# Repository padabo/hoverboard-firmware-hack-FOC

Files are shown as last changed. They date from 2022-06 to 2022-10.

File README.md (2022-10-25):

# hoverboard-firmware-hack-FOC




This repository implements Field Oriented Control (FOC) for stock hoverboards. Compared to the commutation method, this new FOC control method offers superior performance featuring:
 - reduced noise and vibrations 	
 - smooth torque output and improved motor efficiency. Thus, lower energy consumption
 - field weakening to increase maximum speed range

Table of Contents
=======================

* **Wiki:** please check the wiki pages for [Getting Started](https://github.com/EFeru/hoverboard-firmware-hack-FOC/wiki#getting-started) and for [Troubleshooting](https://github.com/EFeru/hoverboard-firmware-hack-FOC/wiki#troubleshooting)
* [Hardware](#hardware)
* [FOC Firmware](#foc-firmware)
* [Example Variants](#example-variants)
* [Projects and Links](#projects-and-links)
* [Contributions](#contributions)

#### The hoverboards with mainboards also come with 2 sideboards(not [splitboards](https://github.com/EFeru/hoverboard-firmware-hack-FOC/wiki/Firmware-Compatibility#split-boards)), check the following [wiki](https://github.com/EFeru/hoverboard-firmware-hack-FOC/wiki/Sideboards) about this firmware

#### For the FOC controller design, see the following repository:
 - [bldc-motor-control-FOC](https://github.com/EFeru/bldc-motor-control-FOC)

#### Videos:
<table>
  <tr>
    <td></td>
    <td></td>
    <td></td>
  </tr>
  <tr>
    <td></td> 
    <td></td>       
    <td></td>
  </tr>
</table>

---
## Hardware
 
mainboard_pinout

The original Hardware supports two 4-pin cables that originally were connected to the two sideboards. They break out GND, 12/15V and USART2&3 of the Hoverboard mainboard. Both USART2&3 support UART, PWM, PPM, and iBUS input. Additionally, the USART2 can be used as 12bit ADC, while USART3 can be used for I2C. Note that while USART3 (right sideboard cable) is 5V tolerant, USART2 (left sideboard cable) is **not** 5V tolerant.

Typically, the mainboard brain is an [STM32F103RCT6](/docs/literature/[10]_STM32F103xC_datasheet.pdf), however some mainboards feature a [GD32F103RCT6](/docs/literature/[11]_GD32F103xx-Datasheet-Rev-2.7.pdf) which is also supported by this firmware.

For the reverse-engineered schematics of the mainboard, see [20150722_hoverboard_sch.pdf](/docs/20150722_hoverboard_sch.pdf)

---
## FOC Firmware
 
In this firmware 3 control types are available, it can be set in config.h file via CTRL_TYP_SEL parameter:
- Commutation (COM_CTRL)
- Sinusoidal (SIN_CTRL)
- Field Oriented Control (FOC_CTRL) with the following 3 control modes that can be set in config.h file with parameter CTRL_MOD_REQ:
  - **VOLTAGE MODE(VLT_MODE)**: in this mode the controller applies a constant Voltage to the motors. Recommended for robotics applications or applications where a fast motor response is required.
  - **SPEED MODE(SPD_MODE)**: in this mode a closed-loop controller realizes the input speed RPM target by rejecting any of the disturbance (resistive load) applied to the motor. Recommended for robotics applications or constant speed applications.
  - **TORQUE MODE(TRQ_MODE)**: in this mode the input torque target is realized. This mode enables motor "freewheeling" when the torque target is `0`. Recommended for most applications with a sitting human driver.

#### Comparison between different control methods

|Control method| Complexity | Efficiency | Smoothness | Field Weakening | Freewheeling | Standstill hold |
|--|--|--|--|--|--|--|
|Commutation| - | - | ++ | n.a. | n.a. | + |
|Sinusoidal| + | ++ | ++ | +++ | n.a. | + |
|FOC VOLTAGE| ++ | +++ | ++ | ++ | n.a. | +<sup>(2)</sup> |
|FOC SPEED| +++ | +++ | + | ++ | n.a. | +++ |
|FOC TORQUE| +++ | +++ | +++ | ++ | +++<sup>(1)</sup> | n.a<sup>(2)</sup> |

<sup>(1)</sup> By enabling `ELECTRIC_BRAKE_ENABLE` in `config.h`, the freewheeling amount can be adjusted using the `ELECTRIC_BRAKE_MAX` parameter.<br/>
<sup>(2)</sup> The standstill hold functionality can be forced by enabling `STANDSTILL_HOLD_ENABLE` in `config.h`. 

In all FOC control modes, the controller features maximum motor speed and maximum motor current protection. This brings great advantages to fulfil the needs of many robotic applications while maintaining safe operation.

### Field Weakening / Phase Advance

 - By default the Field weakening is disabled. You can enable it in config.h file by setting the FIELD_WEAK_ENA = 1 
 - The Field Weakening is a linear interpolation from 0 to FIELD_WEAK_MAX or PHASE_ADV_MAX (depeding if FOC or SIN is selected, respectively)
 - The Field Weakening starts engaging at FIELD_WEAK_LO and reaches the maximum value at FIELD_WEAK_HI
 - The figure below shows different possible calibrations for Field Weakening / Phase Advance
 Field Weakening 
 - If you re-calibrate the Field Weakening please take all the safety measures! The motors can spin very fast!

### Parameters
 - All the calibratable motor parameters can be found in the 'BLDC_controller_data.c'. I provided you with an already calibrated controller, but if you feel like fine tuning it feel free to do so 
 - The parameters are represented in Fixed-point data type for a more efficient code execution
 - For calibrating the fixed-point parameters use the [Fixed-Point Viewer](https://github.com/EFeru/FixedPointViewer) tool
 - The controller parameters are given in [this table](https://github.com/EFeru/bldc-motor-control-FOC/blob/master/02_Figures/paramTable.png)

### FOC Webview

To explore the controller without a Matlab/Simulink installation click on the link below:

[https://eferu.github.io/bldc-motor-control-FOC/](https://eferu.github.io/bldc-motor-control-FOC/)

---
## Example Variants

- **VARIANT_ADC**: The motors are controlled by two potentiometers connected to the Left sensor cable (long wired)
- **VARIANT_USART**: The motors are controlled via serial protocol (e.g. on USART3 right sensor cable, the short wired cable). The commands can be sent from an Arduino. Check out the [hoverserial.ino](/Arduino/hoverserial) as an example sketch.
- **VARIANT_NUNCHUK**: Wii Nunchuk offers one hand control for throttle, braking and steering. This was one of the first input device used for electric armchairs or bottle crates.
- **VARIANT_PPM**: RC remote control with PPM Sum signal.
- **VARIANT_PWM**: RC remote control with PWM signal.
- **VARIANT_IBUS**: RC remote control with Flysky iBUS protocol connected to the Left sensor cable.
- **VARIANT_HOVERCAR**: The motors are controlled by two pedals brake and throttle. Reverse is engaged by double tapping on the brake pedal at standstill. See [HOVERCAR wiki](https://github.com/EFeru/hoverboard-firmware-hack-FOC/wiki/Variant-HOVERCAR).
- **VARIANT_HOVERBOARD**: The mainboard reads the two sideboards data. The sideboards need to be flashed with the hacked version. The balancing controller is **not** yet implemented.
- **VARIANT_TRANSPOTTER**: This is for transpotter build, which is a hoverboard based transportation system. For more details on how to build it check [here](https://github.com/NiklasFauth/hoverboard-firmware-hack/wiki/Build-Instruction:-TranspOtter) and [here](https://hackaday.io/project/161891-transpotter-ng).
- **VARIANT_SKATEBOARD**: This is for skateboard build, controlled using an RC remote with PWM signal connected to the right sensor cable.

Of course the firmware can be further customized for other needs or projects.

---
## Projects and Links

- **Original firmware:** [https://github.com/lucysrausch/hoverboard-firmware-hack](https://github.com/lucysrausch/hoverboard-firmware-hack)
- **[Candas](https://github.com/Candas1/) Hoverboard Web Serial Control:** [https://github.com/Candas1/Hoverboard-Web-Serial-Control](https://github.com/Candas1/Hoverboard-Web-Serial-Control)
- **[RoboDurden's](https://github.com/RoboDurden) online compiler:** [https://pionierland.de/hoverhack/](https://pionierland.de/hoverhack/) 
- **Hoverboard hack for AT32F403RCT6 mainboards:** [https://github.com/cloidnerux/hoverboard-firmware-hack](https://github.com/cloidnerux/hoverboard-firmware-hack)
- **Hoverboard hack for split mainboards:** [https://github.com/flo199213/Hoverboard-Firmware-Hack-Gen2](https://github.com/flo199213/Hoverboard-Firmware-Hack-Gen2)
- **Hoverboard hack from BiPropellant:** [https://github.com/bipropellant](https://github.com/bipropellant)
- **Hoverboard breakout boards:** [https://github.com/Jana-Marie/hoverboard-breakout](https://github.com/Jana-Marie/hoverboard-breakout)

<a/>

- **Bobbycar** [https://github.com/larsmm/hoverboard-firmware-hack-FOC-bbcar](https://github.com/larsmm/hoverboard-firmware-hack-FOC-bbcar)
- **Wheel chair:** [https://github.com/Lahorde/steer_speed_ctrl](https://github.com/Lahorde/steer_speed_ctrl)
- **TranspOtterNG:** [https://github.com/Jan--Henrik/transpOtterNG](https://github.com/Jan--Henrik/transpOtterNG)
- **Hoverboard driver for ROS:** [https://github.com/alex-makarov/hoverboard-driver](https://github.com/alex-makarov/hoverboard-driver)
- **Ongoing OneWheel project:** [https://forum.esk8.news/t/yet-another-hoverboard-to-onewheel-project/60979/14](https://forum.esk8.news/t/yet-another-hoverboard-to-onewheel-project/60979/14)
- **ST Community:** [Custom FOC motor control](https://community.st.com/s/question/0D50X0000B28qTDSQY/custom-foc-control-current-measurement-dma-timer-interrupt-needs-review)

<a/>

- **Telegram Community:** If you are an enthusiast join our [Hooover Telegram Group](https://t.me/joinchat/BHWO_RKu2LT5ZxEkvUB8uw)

---
## Stargazers

Stargazers over time (https://starchart.cc/EFeru/hoverboard-firmware-hack-FOC)

---
## Contributions

Every contribution to this repository is highly appreciated! Feel free to create pull requests to improve this firmware as ultimately you are going to help everyone. 

If you want to donate to keep this firmware updated, please use the link below:



---

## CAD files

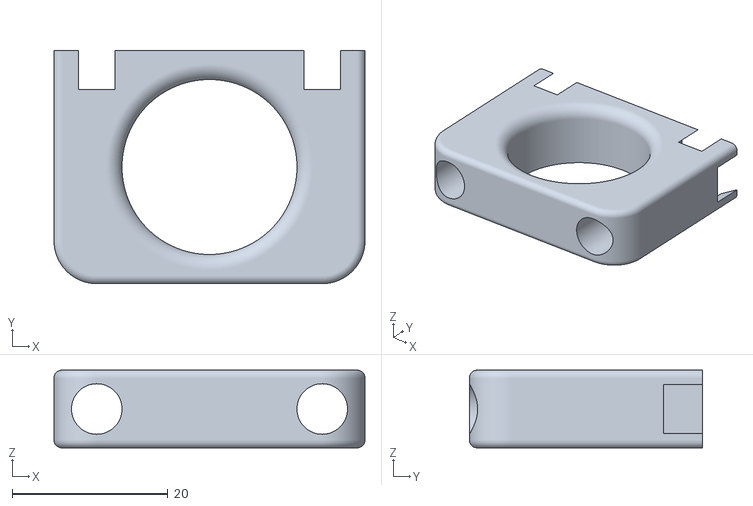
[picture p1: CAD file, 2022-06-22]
Bobbycar STLs/Bobbycar Versteifung x2-x6.stl
40.0 x 30.0 x 10.0

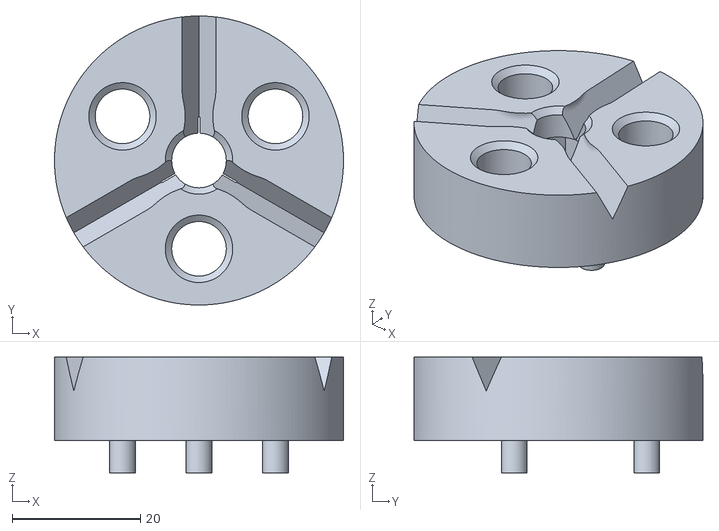
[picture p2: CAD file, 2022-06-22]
Bobbycar STLs/Bobbycar Lenkung Adapter Unten.stl
45.0 x 45.0 x 18.0

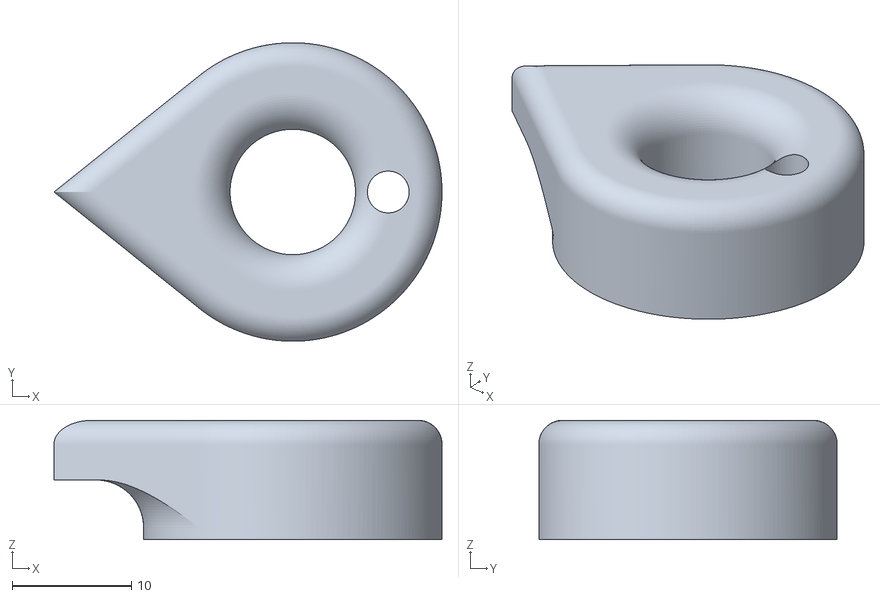
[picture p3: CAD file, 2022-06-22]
Bobbycar STLs/Bobbycar Lenkwinkelsensor Bohradapter.stl
32.5 x 25.0 x 10.0

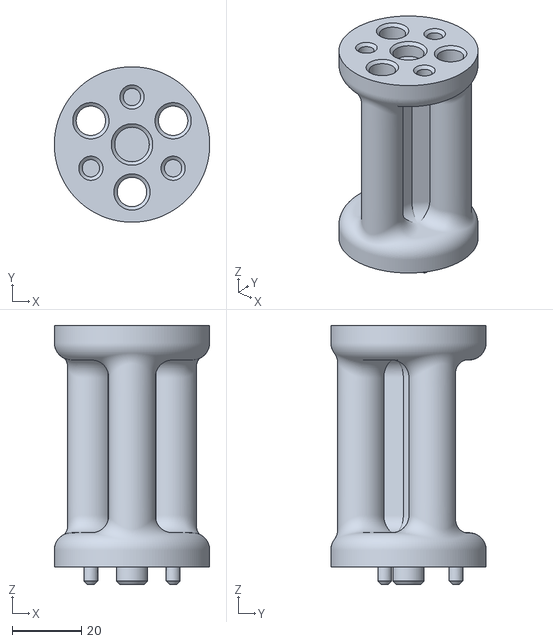
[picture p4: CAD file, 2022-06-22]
Bobbycar STLs/Bobbycar Lenkung Spacer Lang.stl
45.0 x 45.0 x 75.0

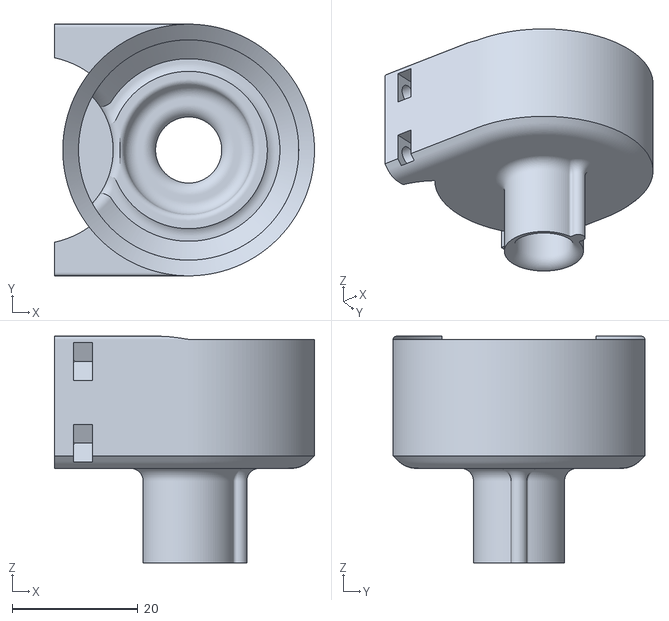
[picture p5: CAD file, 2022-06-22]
Bobbycar STLs/Bobbycar Lenkwinkelsensor Gehäuse.stl
41.3 x 40.0 x 36.0

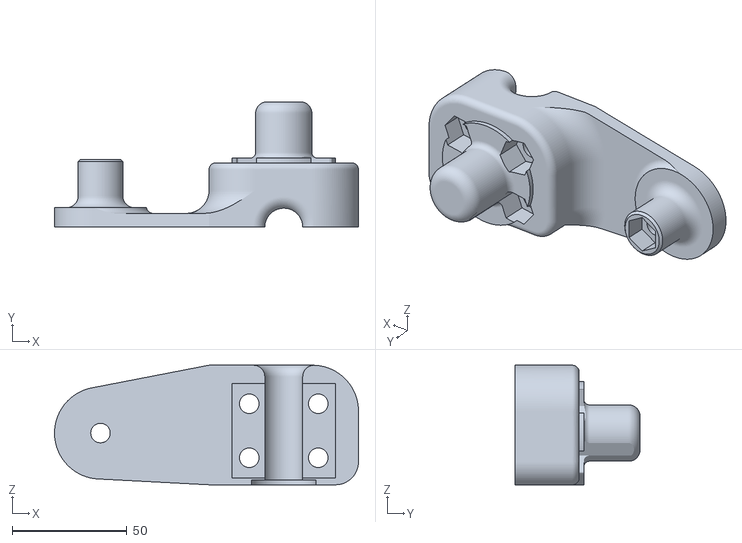
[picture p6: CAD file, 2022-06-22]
Bobbycar STLs/Bobbycar Vorderachse Radaufnahme Oben.stl
132.2 x 54.5 x 52.0

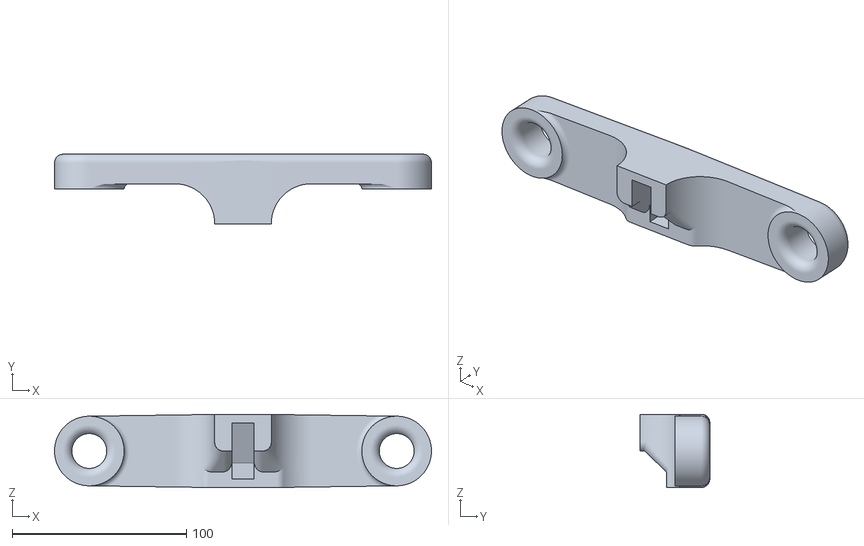
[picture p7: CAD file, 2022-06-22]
Bobbycar STLs/Bobbycar Lenkung Spurstange.stl
216.5 x 40.0 x 42.0

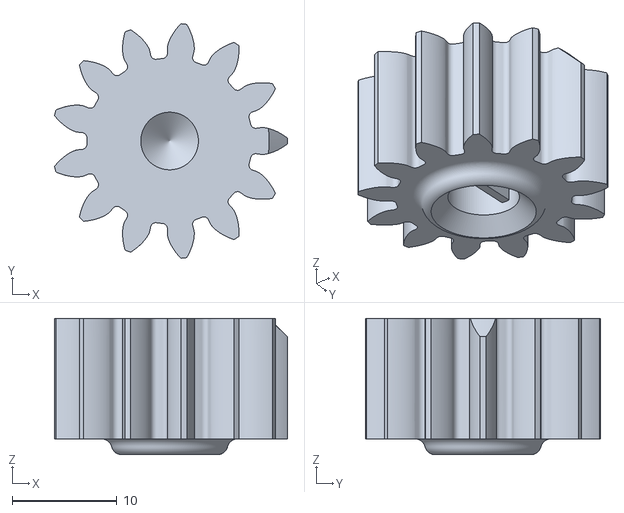
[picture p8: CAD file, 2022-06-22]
Bobbycar STLs/Bobbycar Lenkwinkelsensor Zahnrad Poti.stl
22.2 x 22.4 x 13.0

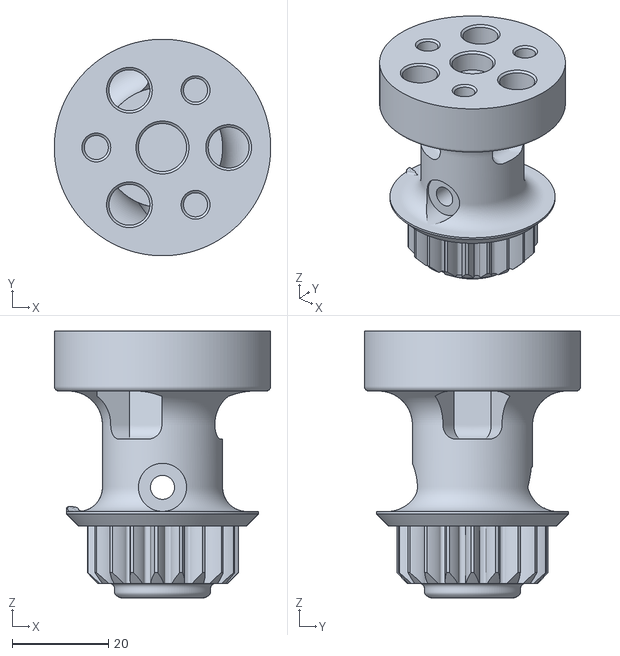
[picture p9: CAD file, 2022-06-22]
Bobbycar STLs/Bobbycar Lenkwinkelsensor Lenkstange.stl
45.0 x 45.0 x 55.5

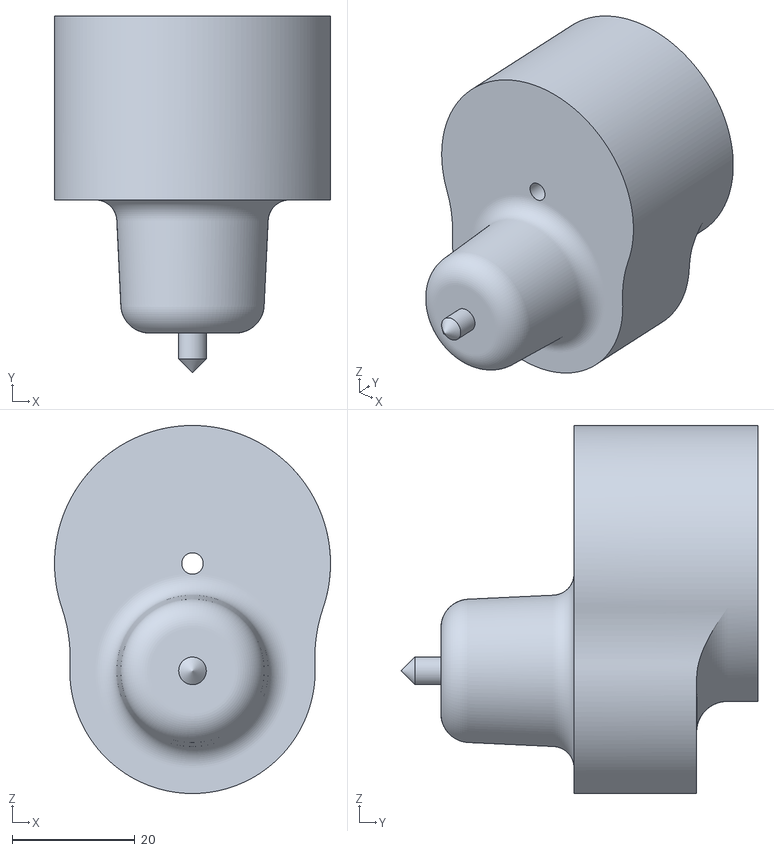
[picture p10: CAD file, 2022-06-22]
Bobbycar STLs/Bobbycar New Adapter x2.stl
45.0 x 58.2 x 60.0

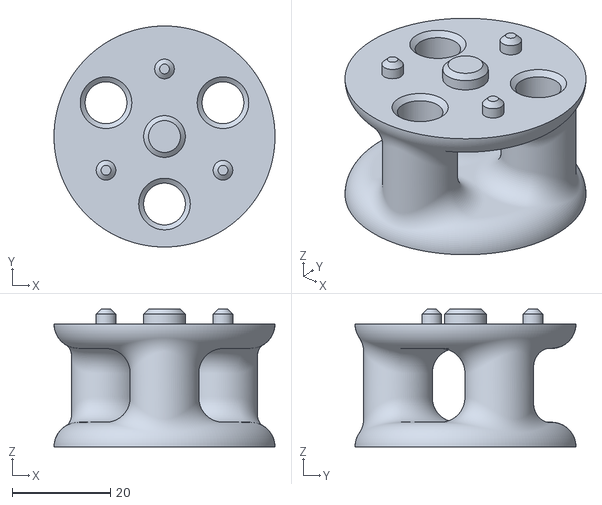
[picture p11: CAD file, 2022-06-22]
Bobbycar STLs/Bobbycar Lenkung Spacer Kurz.stl
45.0 x 45.0 x 28.0

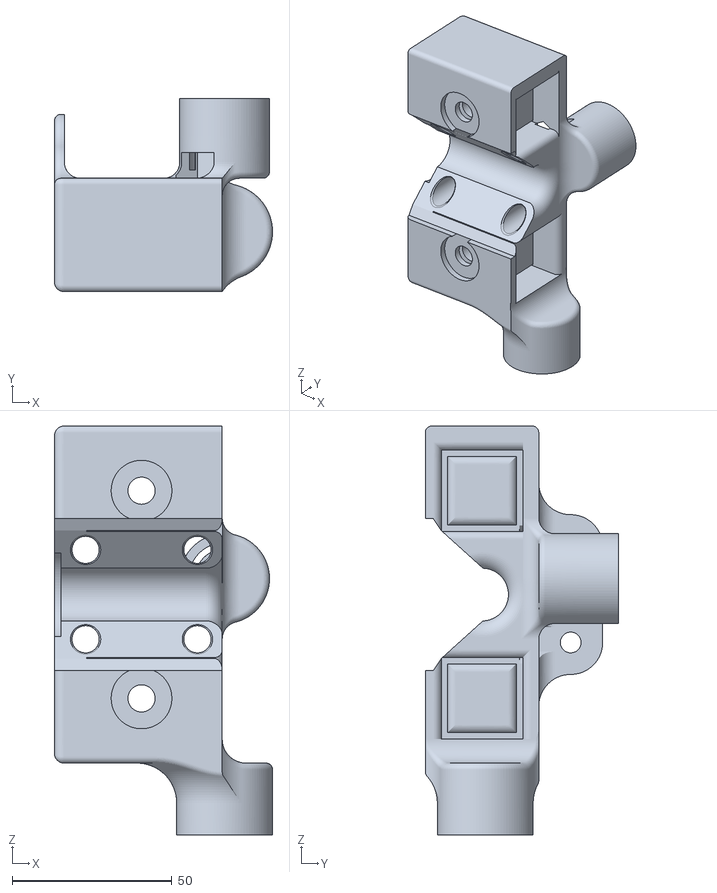
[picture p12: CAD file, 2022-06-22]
Bobbycar STLs/Bobbycar Hinterachse Oben v2.stl
68.2 x 60.5 x 128.0

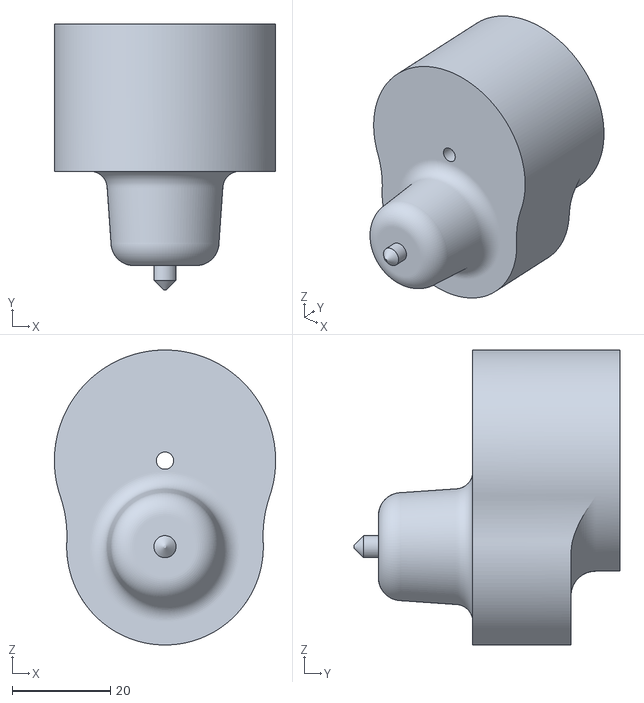
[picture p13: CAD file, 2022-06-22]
Bobbycar STLs/Bobbycar Neo Adapter x2.stl
45.0 x 54.2 x 60.0

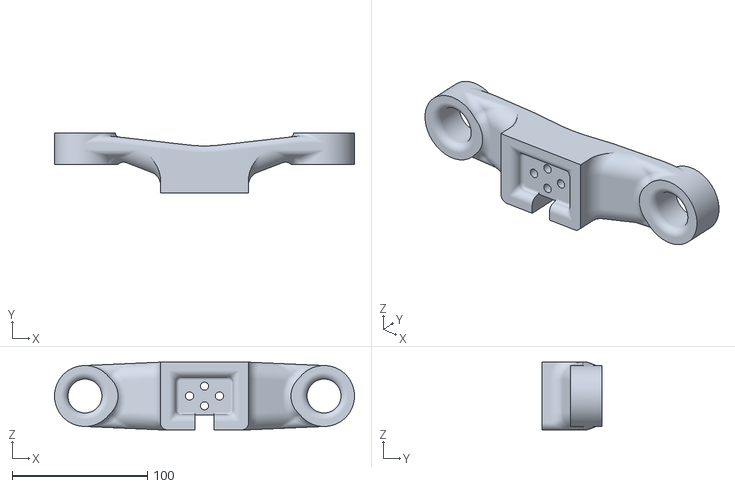
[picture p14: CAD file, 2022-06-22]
Bobbycar STLs/Bobbycar Lenkung Achsschenkel.stl
221.5 x 44.0 x 50.0

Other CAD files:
Bobbycar STLs/Bobbycar Lenkwinkelsensor Potihalter.stl
Bobbycar STLs/Bobbycar Hinterachse Unten.stl
Bobbycar STLs/Bobbycar Lenkung Adapter Oben.stl
Bobbycar STLs/Bobbycar Vorderachse Radaufnahme Unten.stl
Bobbycar STLs/Bobbycar Hinterachse Oben v1.stl

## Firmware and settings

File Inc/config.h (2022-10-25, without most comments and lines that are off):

#define CONFIG_H
#include "stm32f1xx_hal.h"
#if !defined(PLATFORMIO)
  #define VARIANT_USART       // Variant for Serial control via USART3 input
#endif
#define PWM_FREQ            16000     // PWM frequency in Hz / is also used for buzzer
#define DEAD_TIME              48     // PWM deadtime
  #define DELAY_IN_MAIN_LOOP    5     // in ms. default 5. it is independent of all the timing critical stuff. do not touch if you do not know what you are doing.
#define TIMEOUT                20     // number of wrong / missing input commands before emergency off
#define A2BIT_CONV             50     // A to bit for current conversion on ADC. Example: 1 A = 50, 2 A = 100, etc
#define ADC_CONV_TIME_1C5       (14)  //Total ADC clock cycles / conversion = (  1.5+12.5)
#define ADC_CONV_TIME_7C5       (20)  //Total ADC clock cycles / conversion = (  7.5+12.5)
#define ADC_CONV_TIME_13C5      (26)  //Total ADC clock cycles / conversion = ( 13.5+12.5)
#define ADC_CONV_TIME_28C5      (41)  //Total ADC clock cycles / conversion = ( 28.5+12.5)
#define ADC_CONV_TIME_41C5      (54)  //Total ADC clock cycles / conversion = ( 41.5+12.5)
#define ADC_CONV_TIME_55C5      (68)  //Total ADC clock cycles / conversion = ( 55.5+12.5)
#define ADC_CONV_TIME_71C5      (84)  //Total ADC clock cycles / conversion = ( 71.5+12.5)
#define ADC_CONV_TIME_239C5     (252) //Total ADC clock cycles / conversion = (239.5+12.5)
#define ADC_CONV_CLOCK_CYCLES   (ADC_CONV_TIME_7C5)
#define ADC_CLOCK_DIV           (4)
#define ADC_TOTAL_CONV_TIME     (ADC_CLOCK_DIV * ADC_CONV_CLOCK_CYCLES) // = ((SystemCoreClock / ADC_CLOCK_HZ) * ADC_CONV_CLOCK_CYCLES), where ADC_CLOCK_HZ = SystemCoreClock/ADC_CLOCK_DIV
#define BOARD_VARIANT           0         // change if board with alternate pin mapping
#define BAT_FILT_COEF           655       // battery voltage filter coefficient in fixed-point. coef_fixedPoint = coef_floatingPoint * 2^16. In this case 655 = 0.01 * 2^16
#define BAT_CALIB_REAL_VOLTAGE  3970      // input voltage measured by multimeter (multiplied by 100). In this case 43.00 V * 100 = 4300
#define BAT_CALIB_ADC           1492      // adc-value measured by mainboard (value nr 5 on UART debug output)
#define BAT_CELLS               16        // battery number of cells. Normal Hoverboard battery: 10s
#define BAT_LVL2_ENABLE         0         // to beep or not to beep, 1 or 0
#define BAT_LVL1_ENABLE         1         // to beep or not to beep, 1 or 0
#define BAT_DEAD_ENABLE         1         // to poweroff or not to poweroff, 1 or 0
#define BAT_BLINK_INTERVAL      80        // battery led blink interval (80 loops * 5ms ~= 400ms)
#define BAT_LVL5                (390 * BAT_CELLS * BAT_CALIB_ADC) / BAT_CALIB_REAL_VOLTAGE    // Green blink:  no beep
#define BAT_LVL4                (375 * BAT_CELLS * BAT_CALIB_ADC) / BAT_CALIB_REAL_VOLTAGE    // Yellow:       no beep
#define BAT_LVL3                (360 * BAT_CELLS * BAT_CALIB_ADC) / BAT_CALIB_REAL_VOLTAGE    // Yellow blink: no beep
#define BAT_LVL2                (345 * BAT_CELLS * BAT_CALIB_ADC) / BAT_CALIB_REAL_VOLTAGE    // Red:          gently beep at this voltage level. [V*100/cell]. In this case 3.60 V/cell
#define BAT_LVL1                (330 * BAT_CELLS * BAT_CALIB_ADC) / BAT_CALIB_REAL_VOLTAGE    // Red blink:    fast beep. Your battery is almost empty. Charge now! [V*100/cell]. In this case 3.50 V/cell
#define BAT_DEAD                (300 * BAT_CELLS * BAT_CALIB_ADC) / BAT_CALIB_REAL_VOLTAGE    // All leds off: undervoltage poweroff. (while not driving) [V*100/cell]. In this case 3.37 V/cell
#define TEMP_FILT_COEF          655       // temperature filter coefficient in fixed-point. coef_fixedPoint = coef_floatingPoint * 2^16. In this case 655 = 0.01 * 2^16
#define TEMP_CAL_LOW_ADC        1655      // temperature 1: ADC value
#define TEMP_CAL_LOW_DEG_C      358       // temperature 1: measured temperature [°C * 10]. Here 35.8 °C
#define TEMP_CAL_HIGH_ADC       1588      // temperature 2: ADC value
#define TEMP_CAL_HIGH_DEG_C     489       // temperature 2: measured temperature [°C * 10]. Here 48.9 °C
#define TEMP_WARNING_ENABLE     0         // to beep or not to beep, 1 or 0, DO NOT ACTIVITE WITHOUT CALIBRATION!
#define TEMP_WARNING            600       // annoying fast beeps [°C * 10].  Here 60.0 °C
#define TEMP_POWEROFF_ENABLE    0         // to poweroff or not to poweroff, 1 or 0, DO NOT ACTIVITE WITHOUT CALIBRATION!
#define TEMP_POWEROFF           700       // overheat poweroff. (while not driving) [°C * 10]. Here 65.0 °C
#define COM_CTRL        0               // [-] Commutation Control Type
#define SIN_CTRL        1               // [-] Sinusoidal Control Type
#define FOC_CTRL        2               // [-] Field Oriented Control (FOC) Type
#define OPEN_MODE       0               // [-] OPEN mode
#define VLT_MODE        1               // [-] VOLTAGE mode
#define SPD_MODE        2               // [-] SPEED mode
#define TRQ_MODE        3               // [-] TORQUE mode
#define MOTOR_RIGHT_ENA                 // [-] Enable RIGHT motor. Comment-out if this motor is not needed to be operational
#define CTRL_TYP_SEL    FOC_CTRL        // [-] Control type selection: COM_CTRL, SIN_CTRL, FOC_CTRL (default)
#define CTRL_MOD_REQ    TRQ_MODE        // [-] Control mode request: OPEN_MODE, VLT_MODE (default), SPD_MODE, TRQ_MODE. Note: SPD_MODE and TRQ_MODE are only available for CTRL_FOC!
#define DIAG_ENA        1               // [-] Motor Diagnostics enable flag: 0 = Disabled, 1 = Enabled (default)
#define I_MOT_MAX       20              // [A] Maximum single motor current limit
#define I_DC_MAX        25              // [A] Maximum stage2 DC Link current limit for Commutation and Sinusoidal types (This is the final current protection. Above this value, current chopping is applied. To avoid this make sure that I_DC_MAX = I_MOT_MAX + 2A)
#define N_MOT_MAX       2000            // [rpm] Maximum motor speed limit
#define FIELD_WEAK_ENA  1               // [-] Field Weakening / Phase Advance enable flag: 0 = Disabled (default), 1 = Enabled
#define FIELD_WEAK_MAX  10               // [A] Maximum Field Weakening D axis current (only for FOC). Higher current results in higher maximum speed. Up to 10A has been tested using 10" wheels.
#define PHASE_ADV_MAX   25              // [deg] Maximum Phase Advance angle (only for SIN). Higher angle results in higher maximum speed.
#define FIELD_WEAK_HI   1000            // (1000, 1500] Input target High threshold for reaching maximum Field Weakening / Phase Advance. Do NOT set this higher than 1500.
#define FIELD_WEAK_LO   750             // ( 500, 1000] Input target Low threshold for starting Field Weakening / Phase Advance. Do NOT set this higher than 1000.
#define INACTIVITY_TIMEOUT        8       // Minutes of not driving until poweroff. it is not very precise.
#define BEEPS_BACKWARD            1       // 0 or 1
#define ADC_MARGIN                100     // ADC input margin applied on the raw ADC min and max to make sure the MIN and MAX values are reached even in the presence of noise
#define ADC_PROTECT_TIMEOUT       100     // ADC Protection: number of wrong / missing input commands before safety state is taken
#define ADC_PROTECT_THRESH        200     // ADC Protection threshold below/above the MIN/MAX ADC values
#define DEFAULT_RATE                480   // 30.0f [-] lower value == slower rate [0, 32767] = [0.0, 2047.9375]. Do NOT make rate negative (>32767)
#define DEFAULT_FILTER              6553  // Default for FILTER 0.1f [-] lower value == softer filter [0, 65535] = [0.0 - 1.0].
#define DEFAULT_SPEED_COEFFICIENT   16384 // Default for SPEED_COEFFICIENT 1.0f [-] higher value == stronger. [0, 65535] = [-2.0 - 2.0]. In this case 16384 = 1.0 * 2^14
#define DEFAULT_STEER_COEFFICIENT   8192  // Defualt for STEER_COEFFICIENT 0.5f [-] higher value == stronger. [0, 65535] = [-2.0 - 2.0]. In this case  8192 = 0.5 * 2^14. If you do not want any steering, set it to 0.
#define LCD_ADDRESS 0x27
#ifdef VARIANT_USART
  #define CONTROL_SERIAL_USART3  0    // right sensor board cable. Number indicates priority for dual-input. Disable if I2C (nunchuk or lcd) is used! For Arduino control check the hoverSerial.ino
  #define FEEDBACK_SERIAL_USART3      // right sensor board cable, disable if I2C (nunchuk or lcd) is used!
  #define PRI_INPUT1             3, -1000, 0, 1000, 0     // TYPE, MIN, MID, MAX, DEADBAND. See INPUT FORMAT section
  #define PRI_INPUT2             3, -1000, 0, 1000, 0     // TYPE, MIN, MID, MAX, DEADBAND. See INPUT FORMAT section
    #define FLASH_WRITE_KEY      0x1002  // Flash memory writing key. Change this key to ignore the input calibrations from the flash memory and use the ones in config.h
  #define USE_RAW_INPUT
  #define TANK_STEERING              // use for tank steering, each input controls each wheel
#endif
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

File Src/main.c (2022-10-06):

/*
* This file is part of the hoverboard-firmware-hack project.
*
* Copyright (C) 2017-2018 Rene Hopf <renehopf@mac.com>
* Copyright (C) 2017-2018 Nico Stute <crinq@crinq.de>
* Copyright (C) 2017-2018 Niklas Fauth <niklas.fauth@kit.fail>
* Copyright (C) 2019-2020 Emanuel FERU <aerdronix@gmail.com>
*
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
* You should have received a copy of the GNU General Public License
* along with this program.  If not, see <http://www.gnu.org/licenses/>.
*/

#include <stdio.h>
#include <stdlib.h> // for abs()
#include "stm32f1xx_hal.h"
#include "defines.h"
#include "setup.h"
#include "config.h"
#include "util.h"
#include "BLDC_controller.h"      /* BLDC's header file */
#include "rtwtypes.h"
#include "comms.h"
#include "crc32.h"

#if defined(DEBUG_I2C_LCD) || defined(SUPPORT_LCD)
#include "hd44780.h"
#endif

void SystemClock_Config(void);

//------------------------------------------------------------------------
// Global variables set externally
//------------------------------------------------------------------------
extern TIM_HandleTypeDef htim_left;
extern TIM_HandleTypeDef htim_right;
extern ADC_HandleTypeDef hadc1;
extern ADC_HandleTypeDef hadc2;
extern volatile adc_buf_t adc_buffer;
#if defined(DEBUG_I2C_LCD) || defined(SUPPORT_LCD)
  extern LCD_PCF8574_HandleTypeDef lcd;
  extern uint8_t LCDerrorFlag;
#endif

extern UART_HandleTypeDef huart2;
extern UART_HandleTypeDef huart3;

volatile uint8_t uart_buf[200];

// Matlab defines - from auto-code generation
//---------------
extern P    rtP_Left;                   /* Block parameters (auto storage) */
extern P    rtP_Right;                  /* Block parameters (auto storage) */
extern ExtY rtY_Left;                   /* External outputs */
extern ExtY rtY_Right;                  /* External outputs */
extern ExtU rtU_Left;                   /* External inputs */
extern ExtU rtU_Right;                  /* External inputs */
//---------------
#ifdef CONTROL_ADC
  #define ADC_MID 2048
  #define THROTTLE_MAX 1000
  #define ADC_MAX 4095
  #define DEAD_ZONE 64
  #define VAL_CNT 2
  #define BUFFERSIZE 256  
uint32_t index_buff_vals[VAL_CNT];
uint32_t buff_vals[VAL_CNT][BUFFERSIZE];
uint32_t cur_buff_val_sum[VAL_CNT];
uint32_t value_buffer(uint32_t in, int val)
{
  cur_buff_val_sum[val] -= buff_vals[val][index_buff_vals[val]];
  cur_buff_val_sum[val] += (buff_vals[val][index_buff_vals[val]] = in);
  index_buff_vals[val] = (index_buff_vals[val] + 1) % (BUFFERSIZE);
  return (cur_buff_val_sum[val] / (BUFFERSIZE));
}

int clean_adc_full(uint32_t inval)
{
  int outval = (int)(inval) - ADC_MID;
  int abs_outval = abs(outval);
  if (abs_outval < (DEAD_ZONE / 2)) // deadzone
    return 0;
  else
    abs_outval -= (DEAD_ZONE / 2);
  if (abs_outval > (ADC_MAX - ADC_MID - DEAD_ZONE * 3 / 2))
    return THROTTLE_MAX * sign(outval);
  return abs_outval * THROTTLE_MAX / (ADC_MAX - ADC_MID - DEAD_ZONE * 3 / 2) * sign(outval);
}

int clean_adc_half(uint32_t inval)
{
  int outval = (uint32_t)inval;
  if (abs(outval) > (ADC_MAX - ((DEAD_ZONE * 3) / 2)))
    return THROTTLE_MAX;
  else if(abs(outval) < (((DEAD_ZONE * 3) / 2)))
    return 0;
  return outval * (THROTTLE_MAX / 2) / (ADC_MAX - DEAD_ZONE * 3);
}

int PowXplusX(int cleaned_adc,int maximum_value)
{
  return ((cleaned_adc * cleaned_adc / maximum_value) * 2 * SIGN(cleaned_adc) * SIGN(maximum_value)  + cleaned_adc) / 3;
}

#endif


extern uint8_t     inIdx;               // input index used for dual-inputs
extern uint8_t     inIdx_prev;
extern InputStruct input1[];            // input structure
extern InputStruct input2[];            // input structure

extern int16_t speedAvg;                // Average measured speed
extern int16_t speedAvgAbs;             // Average measured speed in absolute
extern volatile uint32_t timeoutCntGen; // Timeout counter for the General timeout (PPM, PWM, Nunchuk)
extern volatile uint8_t  timeoutFlgGen; // Timeout Flag for the General timeout (PPM, PWM, Nunchuk)
extern uint8_t timeoutFlgADC;           // Timeout Flag for for ADC Protection: 0 = OK, 1 = Problem detected (line disconnected or wrong ADC data)
extern uint8_t timeoutFlgSerial;        // Timeout Flag for Rx Serial command: 0 = OK, 1 = Problem detected (line disconnected or wrong Rx data)

extern volatile int pwml;               // global variable for pwm left. -1000 to 1000
extern volatile int pwmr;               // global variable for pwm right. -1000 to 1000

extern uint8_t enable;                  // global variable for motor enable

extern int16_t batVoltage;              // global variable for battery voltage

#if defined(SIDEBOARD_SERIAL_USART2)
extern SerialSideboard Sideboard_L;
#endif
#if defined(SIDEBOARD_SERIAL_USART3)
extern SerialSideboard Sideboard_R;
#endif
#if (defined(CONTROL_PPM_LEFT) && defined(DEBUG_SERIAL_USART3)) || (defined(CONTROL_PPM_RIGHT) && defined(DEBUG_SERIAL_USART2))
extern volatile uint16_t ppm_captured_value[PPM_NUM_CHANNELS+1];
#endif
#if (defined(CONTROL_PWM_LEFT) && defined(DEBUG_SERIAL_USART3)) || (defined(CONTROL_PWM_RIGHT) && defined(DEBUG_SERIAL_USART2))
extern volatile uint16_t pwm_captured_ch1_value;
extern volatile uint16_t pwm_captured_ch2_value;
#endif


//------------------------------------------------------------------------
// Global variables set here in main.c
//------------------------------------------------------------------------
uint8_t backwardDrive;
extern volatile uint32_t buzzerTimer;
volatile uint32_t main_loop_counter;
int16_t batVoltageCalib;         // global variable for calibrated battery voltage
int16_t board_temp_deg_c;        // global variable for calibrated temperature in degrees Celsius
int16_t left_dc_curr;            // global variable for Left DC Link current 
int16_t right_dc_curr;           // global variable for Right DC Link current
int16_t dc_curr;                 // global variable for Total DC Link current 
int16_t cmdL;                    // global variable for Left Command 
int16_t cmdR;                    // global variable for Right Command 

//------------------------------------------------------------------------
// Local variables
//------------------------------------------------------------------------
#if defined(FEEDBACK_SERIAL_USART2) || defined(FEEDBACK_SERIAL_USART3)
typedef struct{
  uint16_t  start;
  int16_t   cmd1;
  int16_t   cmd2;
  int16_t   speedR_meas;
  int16_t   speedL_meas;
  int16_t   batVoltage;
  int16_t   boardTemp;
  uint16_t  cmdLed;
  uint16_t  checksumL;
  uint16_t  checksumH;
} SerialFeedback;
static SerialFeedback Feedback;
#endif
#if defined(FEEDBACK_SERIAL_USART2)
static uint8_t sideboard_leds_L;
#endif
#if defined(FEEDBACK_SERIAL_USART3)
static uint8_t sideboard_leds_R;
#endif

#ifdef VARIANT_TRANSPOTTER
  uint8_t  nunchuk_connected;
  extern float    setDistance;  

  static uint8_t  checkRemote = 0;
  static uint16_t distance;
  static float    steering;
  static int      distanceErr;  
  static int      lastDistance = 0;
  static uint16_t transpotter_counter = 0;
#endif

static int16_t    speed;                // local variable for speed. -1000 to 1000
#ifndef VARIANT_TRANSPOTTER
  static int16_t  steer;                // local variable for steering. -1000 to 1000
  static int16_t  steerRateFixdt;       // local fixed-point variable for steering rate limiter
  static int16_t  speedRateFixdt;       // local fixed-point variable for speed rate limiter
  static int32_t  steerFixdt;           // local fixed-point variable for steering low-pass filter
  static int32_t  speedFixdt;           // local fixed-point variable for speed low-pass filter
#endif

static uint32_t    buzzerTimer_prev = 0;
static uint32_t    inactivity_timeout_counter;
static MultipleTap MultipleTapBrake;    // define multiple tap functionality for the Brake pedal

static uint16_t rate = RATE; // Adjustable rate to support multiple drive modes on startup

#ifdef MULTI_MODE_DRIVE
  static uint8_t drive_mode;
  static uint16_t max_speed;
#endif


int main(void) {

  HAL_Init();
  __HAL_RCC_AFIO_CLK_ENABLE();
  HAL_NVIC_SetPriorityGrouping(NVIC_PRIORITYGROUP_4);
  /* System interrupt init*/
  /* MemoryManagement_IRQn interrupt configuration */
  HAL_NVIC_SetPriority(MemoryManagement_IRQn, 0, 0);
  /* BusFault_IRQn interrupt configuration */
  HAL_NVIC_SetPriority(BusFault_IRQn, 0, 0);
  /* UsageFault_IRQn interrupt configuration */
  HAL_NVIC_SetPriority(UsageFault_IRQn, 0, 0);
  /* SVCall_IRQn interrupt configuration */
  HAL_NVIC_SetPriority(SVCall_IRQn, 0, 0);
  /* DebugMonitor_IRQn interrupt configuration */
  HAL_NVIC_SetPriority(DebugMonitor_IRQn, 0, 0);
  /* PendSV_IRQn interrupt configuration */
  HAL_NVIC_SetPriority(PendSV_IRQn, 0, 0);
  /* SysTick_IRQn interrupt configuration */
  HAL_NVIC_SetPriority(SysTick_IRQn, 0, 0);

  SystemClock_Config();

  __HAL_RCC_DMA1_CLK_DISABLE();
  MX_GPIO_Init();
  MX_TIM_Init();
  MX_ADC1_Init();
  MX_ADC2_Init();
  BLDC_Init();        // BLDC Controller Init

  HAL_GPIO_WritePin(OFF_PORT, OFF_PIN, GPIO_PIN_SET);   // Activate Latch
  Input_Lim_Init();   // Input Limitations Init
  Input_Init();       // Input Init

  HAL_ADC_Start(&hadc1);
  HAL_ADC_Start(&hadc2);

  poweronMelody();
  HAL_GPIO_WritePin(LED_PORT, LED_PIN, GPIO_PIN_SET);
  
  int32_t board_temp_adcFixdt = adc_buffer.temp << 16;  // Fixed-point filter output initialized with current ADC converted to fixed-point
  int16_t board_temp_adcFilt  = adc_buffer.temp;

  #ifdef CONTROL_ADC
    for (int i = 0; i < VAL_CNT; i++)
    {
      cur_buff_val_sum[i] = index_buff_vals[i] = 0;
      for (int j = 0; j < BUFFERSIZE; j++)
        cur_buff_val_sum[i] += (buff_vals[i][j] = ADC_MID);
    }
  #endif

  #ifdef MULTI_MODE_DRIVE
    if (adc_buffer.l_tx2 > input1[0].min + 50 && adc_buffer.l_rx2 > input2[0].min + 50) {
      drive_mode = 2;
      max_speed = MULTI_MODE_DRIVE_M3_MAX;
      rate = MULTI_MODE_DRIVE_M3_RATE;
      rtP_Left.n_max = rtP_Right.n_max = MULTI_MODE_M3_N_MOT_MAX << 4;
      rtP_Left.i_max = rtP_Right.i_max = (MULTI_MODE_M3_I_MOT_MAX * A2BIT_CONV) << 4;
    } else if (adc_buffer.l_tx2 > input1[0].min + 50) {
      drive_mode = 1;
      max_speed = MULTI_MODE_DRIVE_M2_MAX;
      rate = MULTI_MODE_DRIVE_M2_RATE;
      rtP_Left.n_max = rtP_Right.n_max = MULTI_MODE_M2_N_MOT_MAX << 4;
      rtP_Left.i_max = rtP_Right.i_max = (MULTI_MODE_M2_I_MOT_MAX * A2BIT_CONV) << 4;
    } else {
      drive_mode = 0;
      max_speed = MULTI_MODE_DRIVE_M1_MAX;
      rate = MULTI_MODE_DRIVE_M1_RATE;
      rtP_Left.n_max = rtP_Right.n_max = MULTI_MODE_M1_N_MOT_MAX << 4;
      rtP_Left.i_max = rtP_Right.i_max = (MULTI_MODE_M1_I_MOT_MAX * A2BIT_CONV) << 4;
    }

    printf("Drive mode %i selected: max_speed:%i acc_rate:%i \r\n", drive_mode, max_speed, rate);
  #endif

  // Loop until button is released
  while(HAL_GPIO_ReadPin(BUTTON_PORT, BUTTON_PIN)) { HAL_Delay(10); }

  #ifdef MULTI_MODE_DRIVE
    // Wait until triggers are released
    while((adc_buffer.l_rx2 + adc_buffer.l_tx2) >= (input1[0].min + input2[0].min)) { HAL_Delay(10); }
  #endif

  while(1) {
    if (buzzerTimer - buzzerTimer_prev > 16*DELAY_IN_MAIN_LOOP) {   // 1 ms = 16 ticks buzzerTimer

    readCommand();                        // Read Command: input1[inIdx].cmd, input2[inIdx].cmd
    calcAvgSpeed();                       // Calculate average measured speed: speedAvg, speedAvgAbs

    #ifndef VARIANT_TRANSPOTTER
      // ####### MOTOR ENABLING: Only if the initial input is very small (for SAFETY) #######
      if (enable == 0 && !rtY_Left.z_errCode && !rtY_Right.z_errCode && 
          ABS(input1[inIdx].cmd) < 50 && ABS(input2[inIdx].cmd) < 50){
        beepShort(6);                     // make 2 beeps indicating the motor enable
        beepShort(4); HAL_Delay(100);
        steerFixdt = speedFixdt = 0;      // reset filters
        enable = 1;                       // enable motors
        #if defined(DEBUG_SERIAL_USART2) || defined(DEBUG_SERIAL_USART3)
        printf("-- Motors enabled --\r\n");
        #endif
      }

      // ####### VARIANT_HOVERCAR #######
      #if defined(VARIANT_HOVERCAR) || defined(VARIANT_SKATEBOARD) || defined(ELECTRIC_BRAKE_ENABLE)
        uint16_t speedBlend;                                        // Calculate speed Blend, a number between [0, 1] in fixdt(0,16,15)
        speedBlend = (uint16_t)(((CLAMP(speedAvgAbs,10,60) - 10) << 15) / 50); // speedBlend [0,1] is within [10 rpm, 60rpm]
      #endif

      #ifdef STANDSTILL_HOLD_ENABLE
        standstillHold();                                           // Apply Standstill Hold functionality. Only available and makes sense for VOLTAGE or TORQUE Mode
      #endif

      #ifdef VARIANT_HOVERCAR
      if (inIdx == CONTROL_ADC) {                                   // Only use use implementation below if pedals are in use (ADC input)
        if (speedAvgAbs < 60) {                                     // Check if Hovercar is physically close to standstill to enable Double tap detection on Brake pedal for Reverse functionality
          multipleTapDet(input1[inIdx].cmd, HAL_GetTick(), &MultipleTapBrake); // Brake pedal in this case is "input1" variable
        }

        if (input1[inIdx].cmd > 30) {                               // If Brake pedal (input1) is pressed, bring to 0 also the Throttle pedal (input2) to avoid "Double pedal" driving
          input2[inIdx].cmd = (int16_t)((input2[inIdx].cmd * speedBlend) >> 15);
          cruiseControl((uint8_t)rtP_Left.b_cruiseCtrlEna);         // Cruise control deactivated by Brake pedal if it was active
        }
      }
      #endif

      #ifdef ELECTRIC_BRAKE_ENABLE
        electricBrake(speedBlend, MultipleTapBrake.b_multipleTap);  // Apply Electric Brake. Only available and makes sense for TORQUE Mode
      #endif

      #ifdef VARIANT_HOVERCAR
      if (inIdx == CONTROL_ADC) {                                   // Only use use implementation below if pedals are in use (ADC input)
        if (speedAvg > 0) {                                         // Make sure the Brake pedal is opposite to the direction of motion AND it goes to 0 as we reach standstill (to avoid Reverse driving by Brake pedal) 
          input1[inIdx].cmd = (int16_t)((-input1[inIdx].cmd * speedBlend) >> 15);
        } else {
          input1[inIdx].cmd = (int16_t)(( input1[inIdx].cmd * speedBlend) >> 15);
        }
      }
      #endif

      #ifdef VARIANT_SKATEBOARD
        if (input2[inIdx].cmd < 0) {                                // When Throttle is negative, it acts as brake. This condition is to make sure it goes to 0 as we reach standstill (to avoid Reverse driving) 
          if (speedAvg > 0) {                                       // Make sure the braking is opposite to the direction of motion
            input2[inIdx].cmd  = (int16_t)(( input2[inIdx].cmd * speedBlend) >> 15);
          } else {
            input2[inIdx].cmd  = (int16_t)((-input2[inIdx].cmd * speedBlend) >> 15);
          }
        }
      #endif

      #ifndef USE_RAW_INPUT
      // ####### LOW-PASS FILTER #######
      rateLimiter16(input1[inIdx].cmd, rate, &steerRateFixdt);
      rateLimiter16(input2[inIdx].cmd, rate, &speedRateFixdt);
      filtLowPass32(steerRateFixdt >> 4, FILTER, &steerFixdt);
      filtLowPass32(speedRateFixdt >> 4, FILTER, &speedFixdt);
      steer = (int16_t)(steerFixdt >> 16);  // convert fixed-point to integer
      speed = (int16_t)(speedFixdt >> 16);  // convert fixed-point to integer
      #else
      steer = input1[inIdx].raw;  // convert fixed-point to integer
      speed = input2[inIdx].raw;  // convert fixed-point to integer
      #endif
      // ####### VARIANT_HOVERCAR #######
      #ifdef VARIANT_HOVERCAR
      if (inIdx == CONTROL_ADC) {               // Only use use implementation below if pedals are in use (ADC input)

        #ifdef MULTI_MODE_DRIVE
        if (speed >= max_speed) {
          speed = max_speed;
        }
        #endif

        if (!MultipleTapBrake.b_multipleTap) {  // Check driving direction
          speed = steer + speed;                // Forward driving: in this case steer = Brake, speed = Throttle
        } else {
          speed = steer - speed;                // Reverse driving: in this case steer = Brake, speed = Throttle
        }
        steer = 0;                              // Do not apply steering to avoid side effects if STEER_COEFFICIENT is NOT 0
      }
      #endif

      #if defined(TANK_STEERING) && !defined(VARIANT_HOVERCAR) && !defined(VARIANT_SKATEBOARD) 
        // Tank steering (no mixing)
        cmdL = steer; 
        cmdR = speed;
      #else 
        // ####### MIXER #######
        mixerFcn(speed << 4, steer << 4, &cmdR, &cmdL);   // This function implements the equations above
      #endif


      // ####### SET OUTPUTS (if the target change is less than +/- 100) #######
      #ifdef INVERT_R_DIRECTION
        pwmr = cmdR;
      #else
        pwmr = -cmdR;
      #endif
      #ifdef INVERT_L_DIRECTION
        pwml = -cmdL;
      #else
        pwml = cmdL;
      #endif
    #endif

    #ifdef VARIANT_TRANSPOTTER
      distance    = CLAMP(input1[inIdx].cmd - 180, 0, 4095);
      steering    = (input2[inIdx].cmd - 2048) / 2048.0;
      distanceErr = distance - (int)(setDistance * 1345);

      if (nunchuk_connected == 0) {
        cmdL = cmdL * 0.8f + (CLAMP(distanceErr + (steering*((float)MAX(ABS(distanceErr), 50)) * ROT_P), -850, 850) * -0.2f);
        cmdR = cmdR * 0.8f + (CLAMP(distanceErr - (steering*((float)MAX(ABS(distanceErr), 50)) * ROT_P), -850, 850) * -0.2f);
        if (distanceErr > 0) {
          enable = 1;
        }
        if (distanceErr > -300) {
          #ifdef INVERT_R_DIRECTION
            pwmr = cmdR;
          #else
            pwmr = -cmdR;
          #endif
          #ifdef INVERT_L_DIRECTION
            pwml = -cmdL;
          #else
            pwml = cmdL;
          #endif

          if (checkRemote) {
            if (!HAL_GPIO_ReadPin(LED_PORT, LED_PIN)) {
              //enable = 1;
            } else {
              enable = 0;
            }
          }
        } else {
          enable = 0;
        }
        timeoutCntGen = 0;
        timeoutFlgGen = 0;
      }

      if (timeoutFlgGen) {
        pwml = 0;
        pwmr = 0;
        enable = 0;
        #ifdef SUPPORT_LCD
          LCD_SetLocation(&lcd,  0, 0); LCD_WriteString(&lcd, "Len:");
          LCD_SetLocation(&lcd,  8, 0); LCD_WriteString(&lcd, "m(");
          LCD_SetLocation(&lcd, 14, 0); LCD_WriteString(&lcd, "m)");
        #endif
        HAL_Delay(1000);
        nunchuk_connected = 0;
      }

      if ((distance / 1345.0) - setDistance > 0.5 && (lastDistance / 1345.0) - setDistance > 0.5) { // Error, robot too far away!
        enable = 0;
        beepLong(5);
        #ifdef SUPPORT_LCD
          LCD_ClearDisplay(&lcd);
          HAL_Delay(5);
          LCD_SetLocation(&lcd, 0, 0); LCD_WriteString(&lcd, "Emergency Off!");
          LCD_SetLocation(&lcd, 0, 1); LCD_WriteString(&lcd, "Keeper too fast.");
        #endif
        poweroff();
      }

      #ifdef SUPPORT_NUNCHUK
        if (transpotter_counter % 500 == 0) {
          if (nunchuk_connected == 0 && enable == 0) {
              if(Nunchuk_Read() == NUNCHUK_CONNECTED) {
                #ifdef SUPPORT_LCD
                  LCD_SetLocation(&lcd, 0, 0); LCD_WriteString(&lcd, "Nunchuk Control");
                #endif
                nunchuk_connected = 1;
	      }
	    } else {
              nunchuk_connected = 0;
	    }
          }
        }   
      #endif

      #ifdef SUPPORT_LCD
        if (transpotter_counter % 100 == 0) {
          if (LCDerrorFlag == 1 && enable == 0) {

          } else {
            if (nunchuk_connected == 0) {
              LCD_SetLocation(&lcd,  4, 0); LCD_WriteFloat(&lcd,distance/1345.0,2);
              LCD_SetLocation(&lcd, 10, 0); LCD_WriteFloat(&lcd,setDistance,2);
            }
            LCD_SetLocation(&lcd,  4, 1); LCD_WriteFloat(&lcd,batVoltage, 1);
            // LCD_SetLocation(&lcd, 11, 1); LCD_WriteFloat(&lcd,MAX(ABS(currentR), ABS(currentL)),2);
          }
        }
      #endif
      transpotter_counter++;
    #endif

    // ####### SIDEBOARDS HANDLING #######
    #if defined(SIDEBOARD_SERIAL_USART2)
      sideboardSensors((uint8_t)Sideboard_L.sensors);
    #endif
    #if defined(FEEDBACK_SERIAL_USART2)
      sideboardLeds(&sideboard_leds_L);
    #endif
    #if defined(SIDEBOARD_SERIAL_USART3)
      sideboardSensors((uint8_t)Sideboard_R.sensors);
    #endif
    #if defined(FEEDBACK_SERIAL_USART3)
      sideboardLeds(&sideboard_leds_R);
    #endif
    

    // ####### CALC BOARD TEMPERATURE #######
    filtLowPass32(adc_buffer.temp, TEMP_FILT_COEF, &board_temp_adcFixdt);
    board_temp_adcFilt  = (int16_t)(board_temp_adcFixdt >> 16);  // convert fixed-point to integer
    board_temp_deg_c    = (TEMP_CAL_HIGH_DEG_C - TEMP_CAL_LOW_DEG_C) * (board_temp_adcFilt - TEMP_CAL_LOW_ADC) / (TEMP_CAL_HIGH_ADC - TEMP_CAL_LOW_ADC) + TEMP_CAL_LOW_DEG_C;

    // ####### CALC CALIBRATED BATTERY VOLTAGE #######
    batVoltageCalib = batVoltage * BAT_CALIB_REAL_VOLTAGE / BAT_CALIB_ADC;

    // ####### CALC DC LINK CURRENT #######
    left_dc_curr  = -(rtU_Left.i_DCLink * 100) / A2BIT_CONV;   // Left DC Link Current * 100 
    right_dc_curr = -(rtU_Right.i_DCLink * 100) / A2BIT_CONV;  // Right DC Link Current * 100
    dc_curr       = left_dc_curr + right_dc_curr;            // Total DC Link Current * 100
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

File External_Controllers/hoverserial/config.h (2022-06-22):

#define ADC_MIN 0                  // min ADC1-value while poti at minimum-position (0 - 1023)
#define ADC_MAX ((1 << 12) -1)               // max ADC1-value while poti at maximum-position (0 - 1023)
#define ADC_MID (ADC_MAX / 2)
#define DEAD_ZONE 64

#define STEERING_EAGLE_FACTOR (M_PI_4/1000.0f)
#define WHEELBASE 35
#define WHEEL_WIDTH 10
#define STEERING_TO_WHEEL_DIST 5

#define THROTTLE_MAX 1000
#define THROTTLE_REVERSE_MAX (THROTTLE_MAX * 3 / 10)

#define THROTTLE0_PIN 32
#define THROTTLE1_PIN 35
#define STEERING_PIN 33
#define I2C_SDA 22
#define I2C_SCL 23
#define RX0 17
#define TX0 16
#define RX1 18
#define TX1 5
// ########################## DEFINES ##########################
#define HOVER_SERIAL_BAUD 115200 // [-] Baud rate for HoverSerial (used to communicate with the hoverboard)
#define SERIAL_BAUD 115200       // [-] Baud rate for built-in Serial (used for the Serial Monitor)
#define START_FRAME 0xABCD       // [-] Start frame definition for reliable serial communication
#define TIME_SEND 20             // [ms] Sending time interval
// #define DEBUG_RX                        // [-] Debug received data. Prints all bytes to serial (comment-out to disable)

#define SCREEN_ADDRESS 0x3C ///< See datasheet for Address; 0x3D for 128x64, 0x3C for 128x32
#define SCREEN_WIDTH 128 // OLED display width, in pixels
#define SCREEN_HEIGHT 64 // OLED display height, in pixels

#define BUFFERSIZE 256
#define VAL_CNT 3

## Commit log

2022-05-30 display2hal added buzzer profiles
    [bldc.c]
2022-05-30 rework buzzer without beep no life
    [bldc.c]
2022-05-31 update arduino
2022-06-03 esp32 builds
2022-06-13 config usart tank steering
2022-06-22 no uart error
2022-06-22 added bobbycar stl files
    [Bobbycar Hinterachse Oben v1.stl, Bobbycar Hinterachse Oben v2.stl, Bobbycar Hinterachse Unten.stl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]
2022-07-09 new calibration function
2022-07-13 disable calibration
2022-08-01 dirty wakeup for high voltage
2022-08-05 invert motor
2022-09-26 new crc32 for less bus errors
    [main.c, util.c]
2022-09-28 Start Frame

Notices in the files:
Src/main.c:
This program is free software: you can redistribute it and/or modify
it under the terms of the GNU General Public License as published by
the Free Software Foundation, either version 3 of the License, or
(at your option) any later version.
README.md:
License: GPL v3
